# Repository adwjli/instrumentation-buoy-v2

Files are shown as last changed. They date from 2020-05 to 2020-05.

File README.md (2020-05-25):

# Instrumentation Buoy Data Logger - Version 2

A continuation of the [Instrumentation Buoy Data Logger (Version 1)](https://github.com/andrewjunli/instrumentation-buoy-v1) project, Version 2 features a new PCB layout where the electronics of the Main Board and Power Board are combined into one PCB assembly to make it easier to assemble the buoy. Improvements were made to the solar charging circuitry, a new wireless module has been used and the LED safety light has been redesigned. Also for the first time, I've published the full technical documentation of this design as a learning and reference resource for other hardware designers.

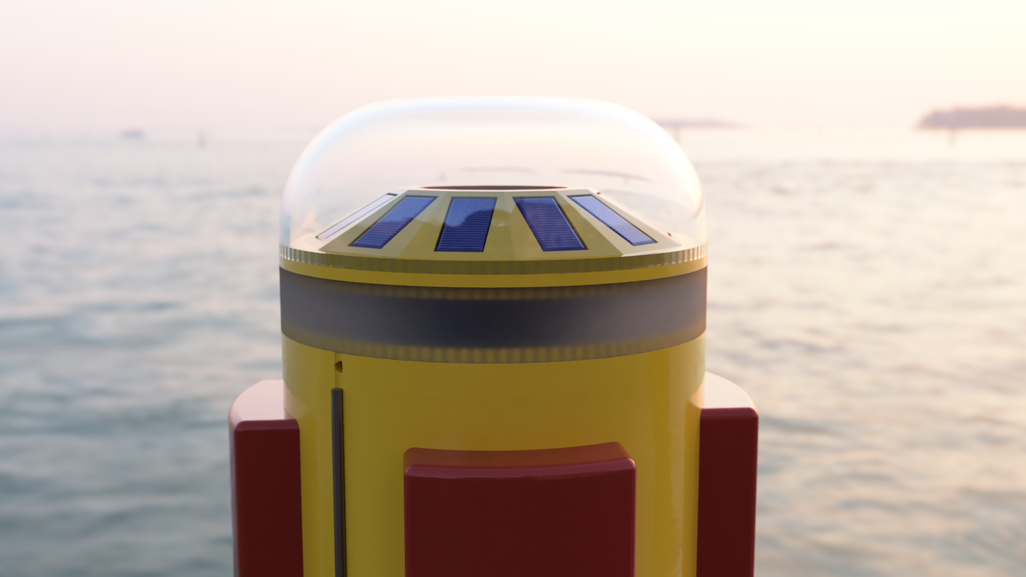
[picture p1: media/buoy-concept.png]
Buoy concept.


The imagery shown above is a concept design of the new buoy prototype.

## Technical Documentation

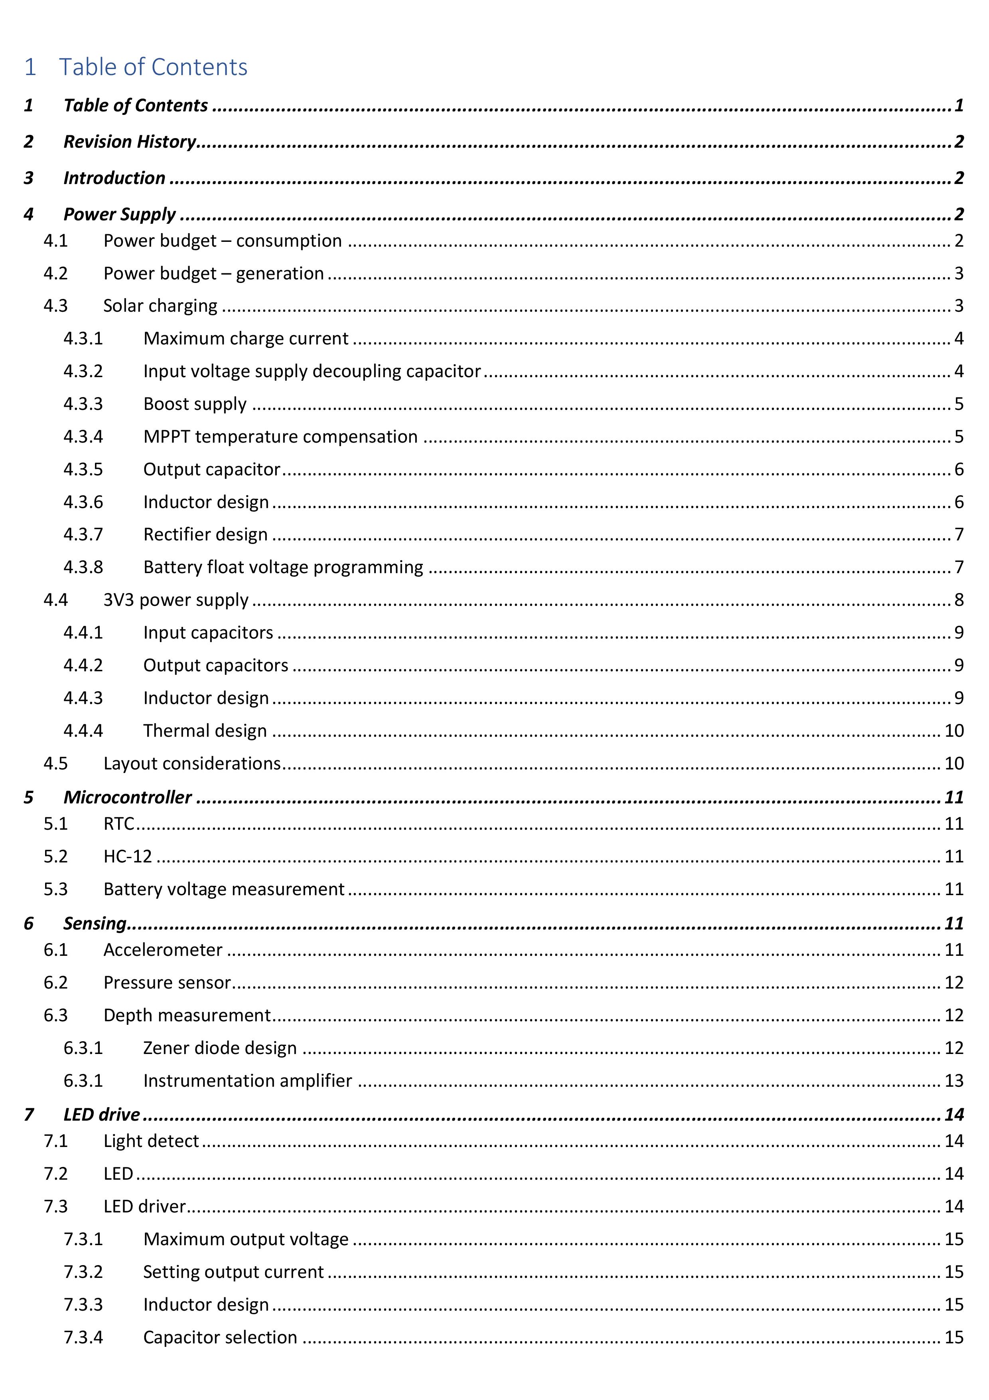
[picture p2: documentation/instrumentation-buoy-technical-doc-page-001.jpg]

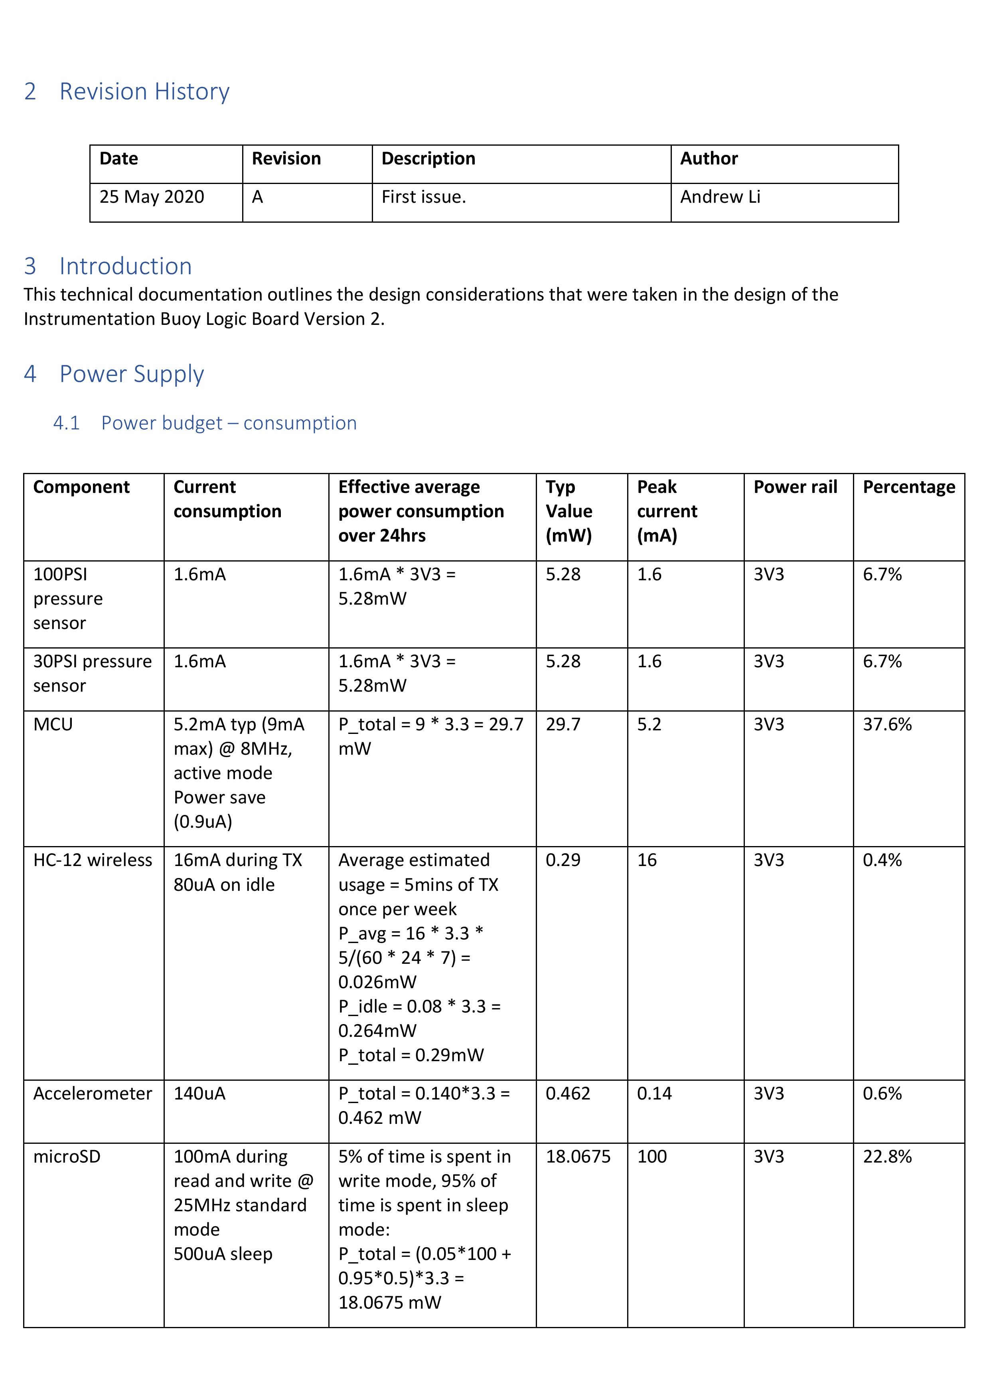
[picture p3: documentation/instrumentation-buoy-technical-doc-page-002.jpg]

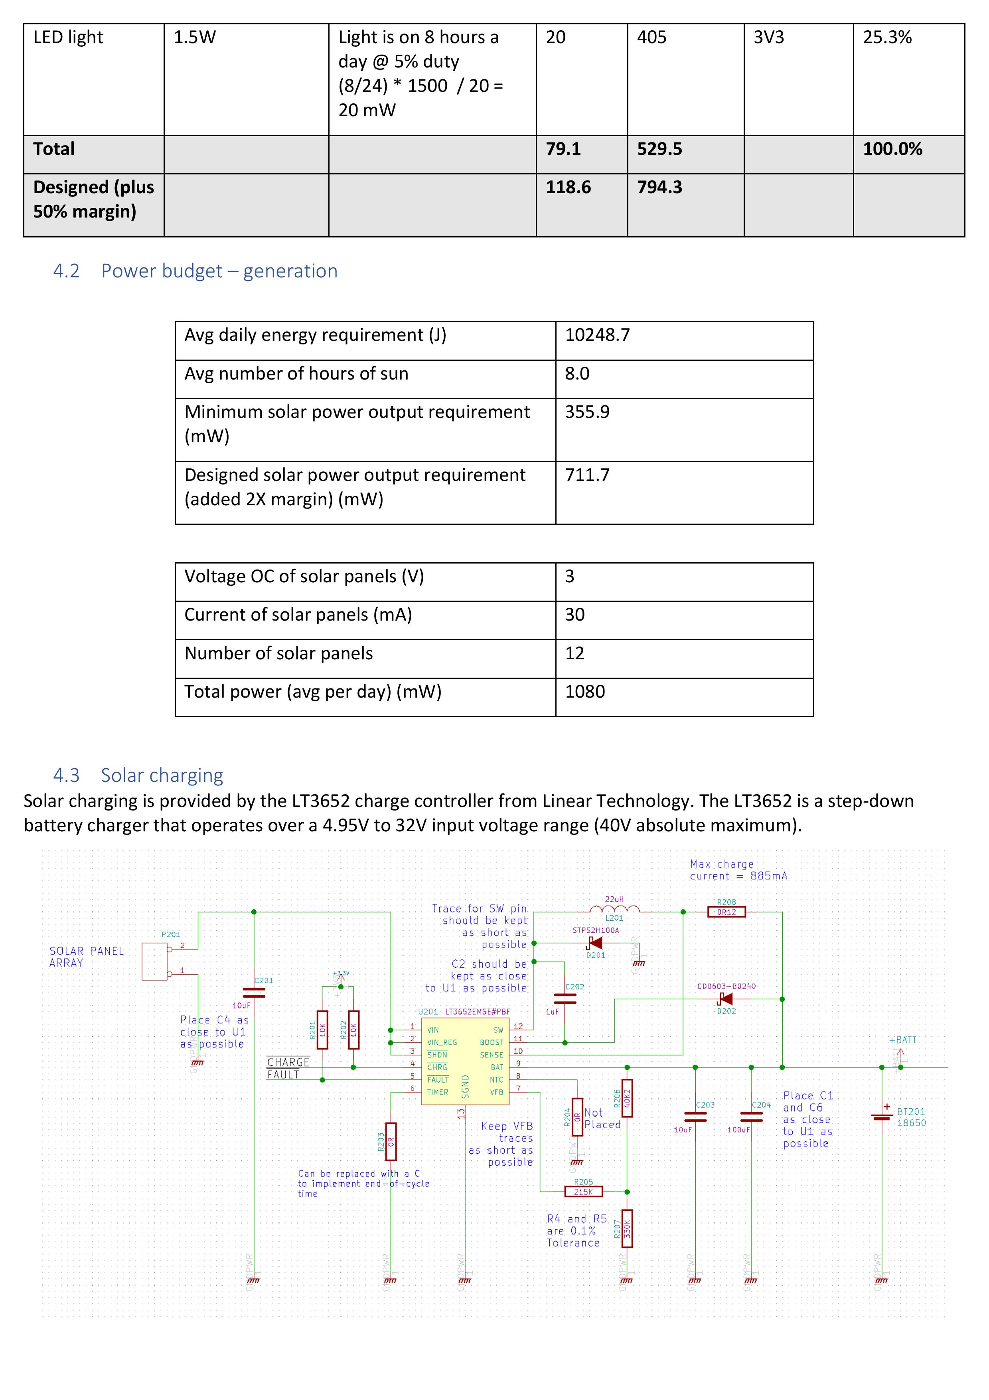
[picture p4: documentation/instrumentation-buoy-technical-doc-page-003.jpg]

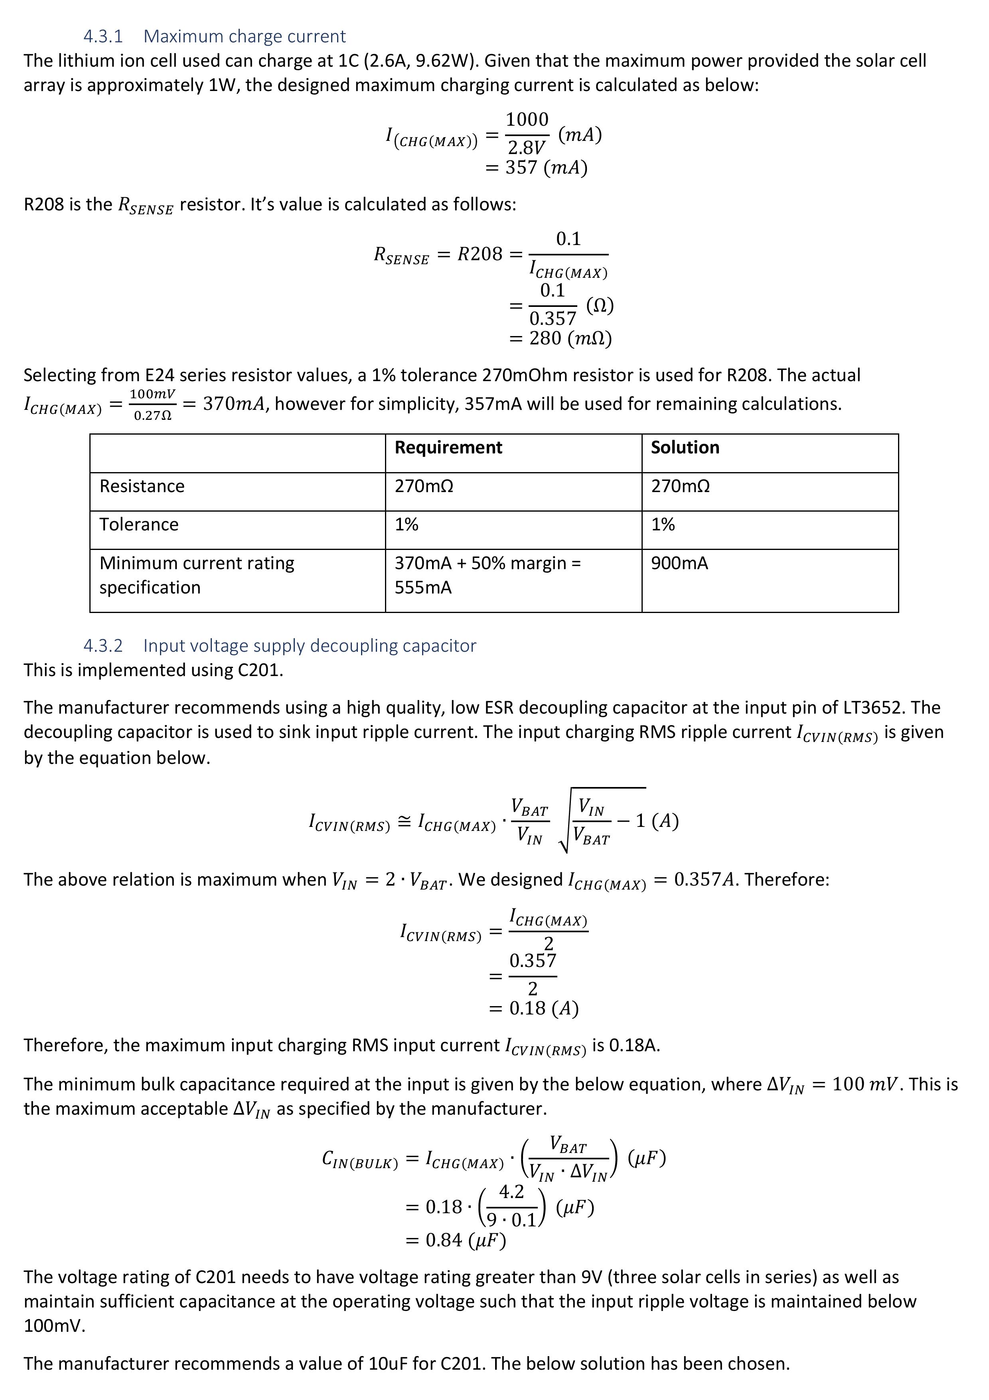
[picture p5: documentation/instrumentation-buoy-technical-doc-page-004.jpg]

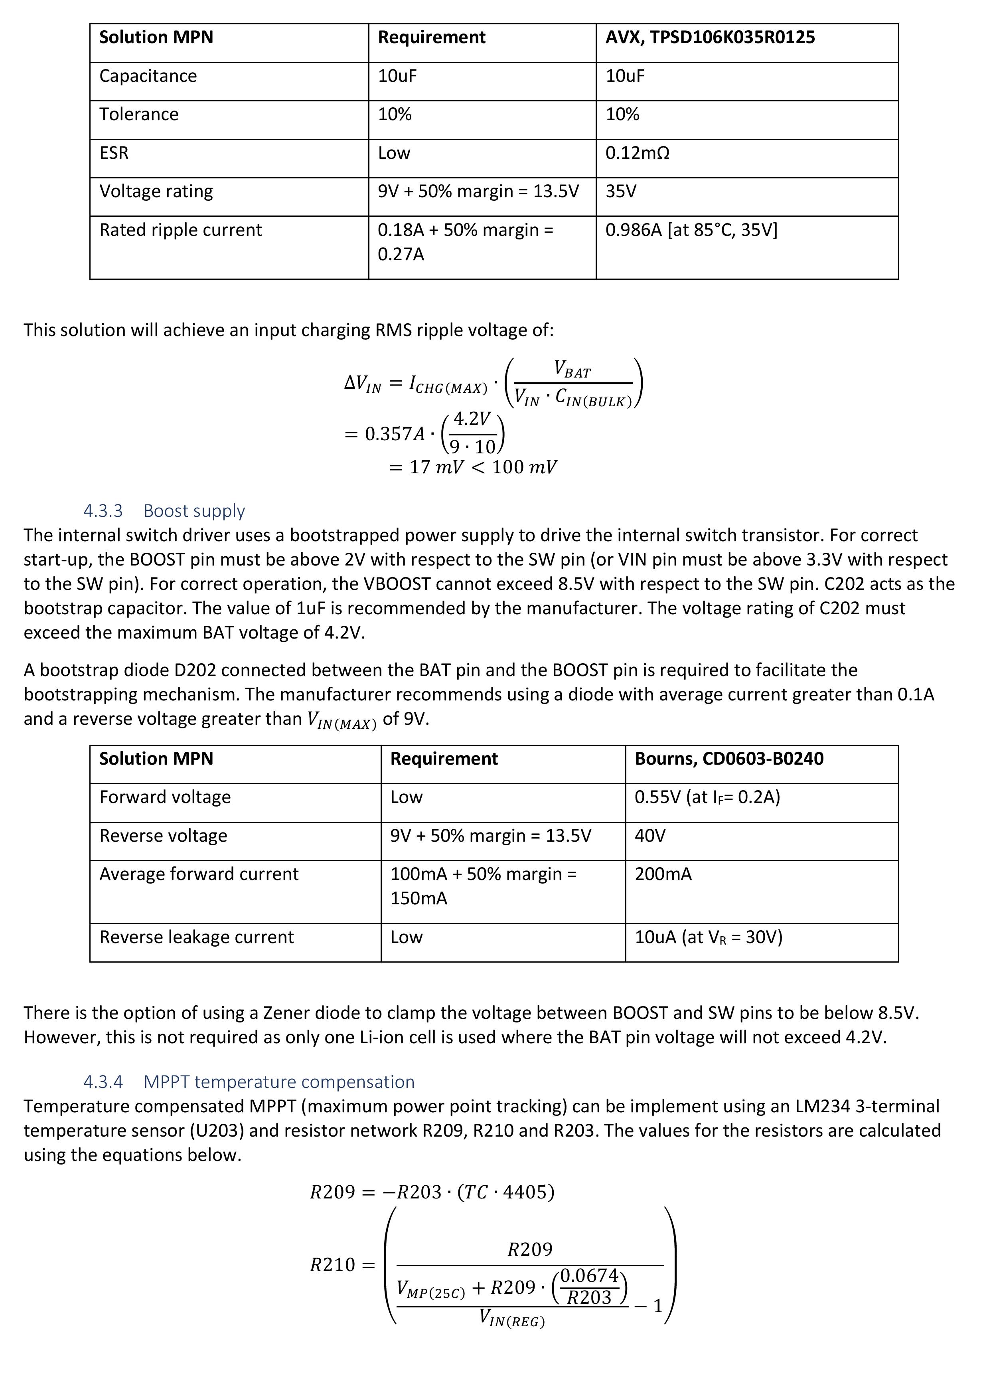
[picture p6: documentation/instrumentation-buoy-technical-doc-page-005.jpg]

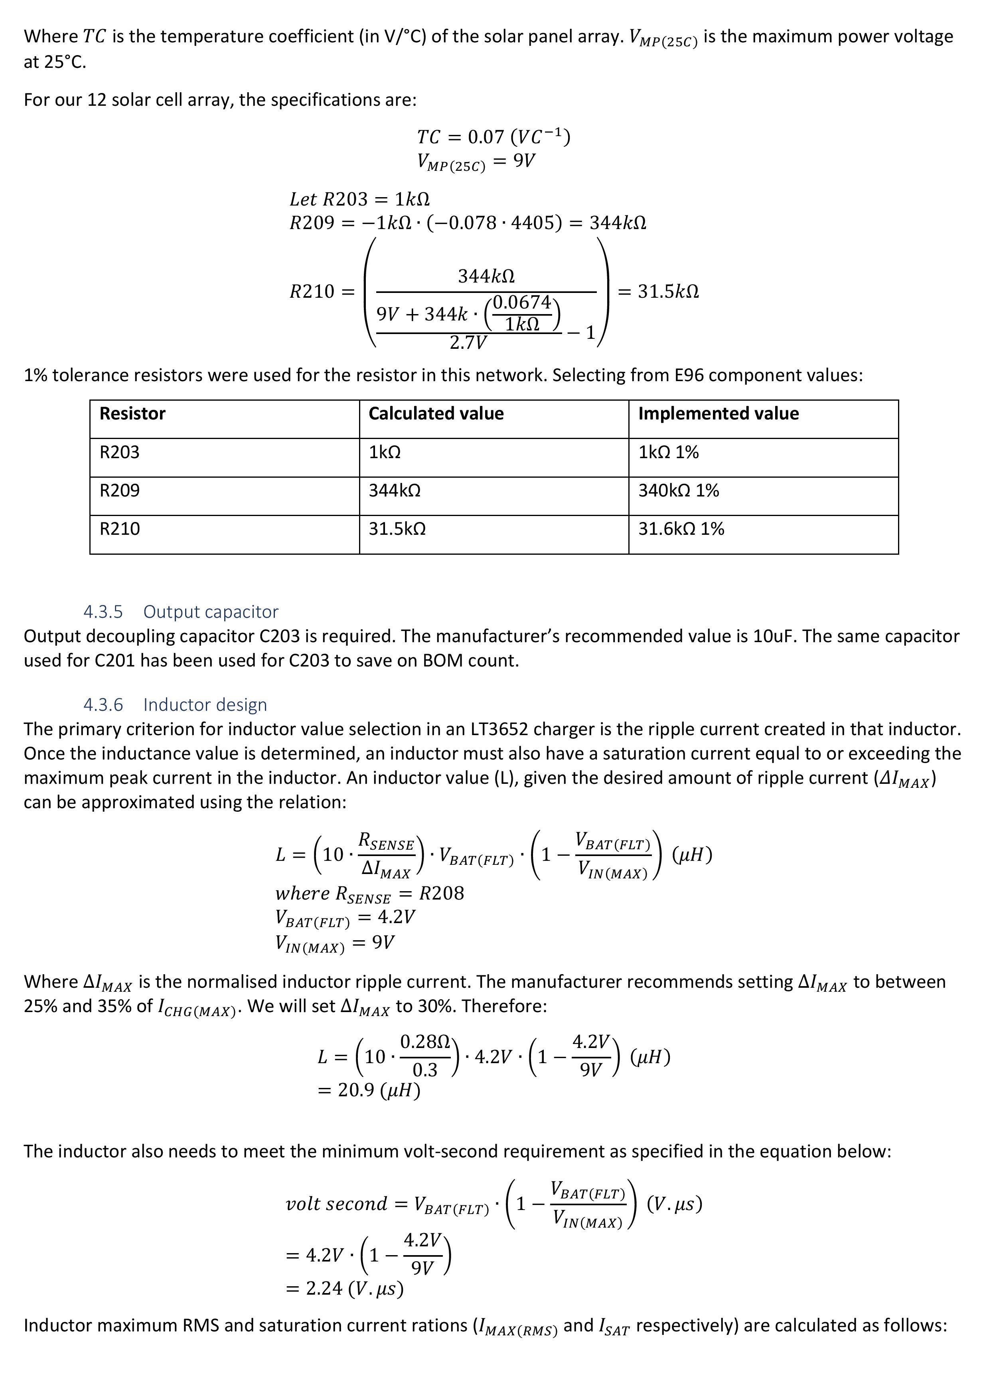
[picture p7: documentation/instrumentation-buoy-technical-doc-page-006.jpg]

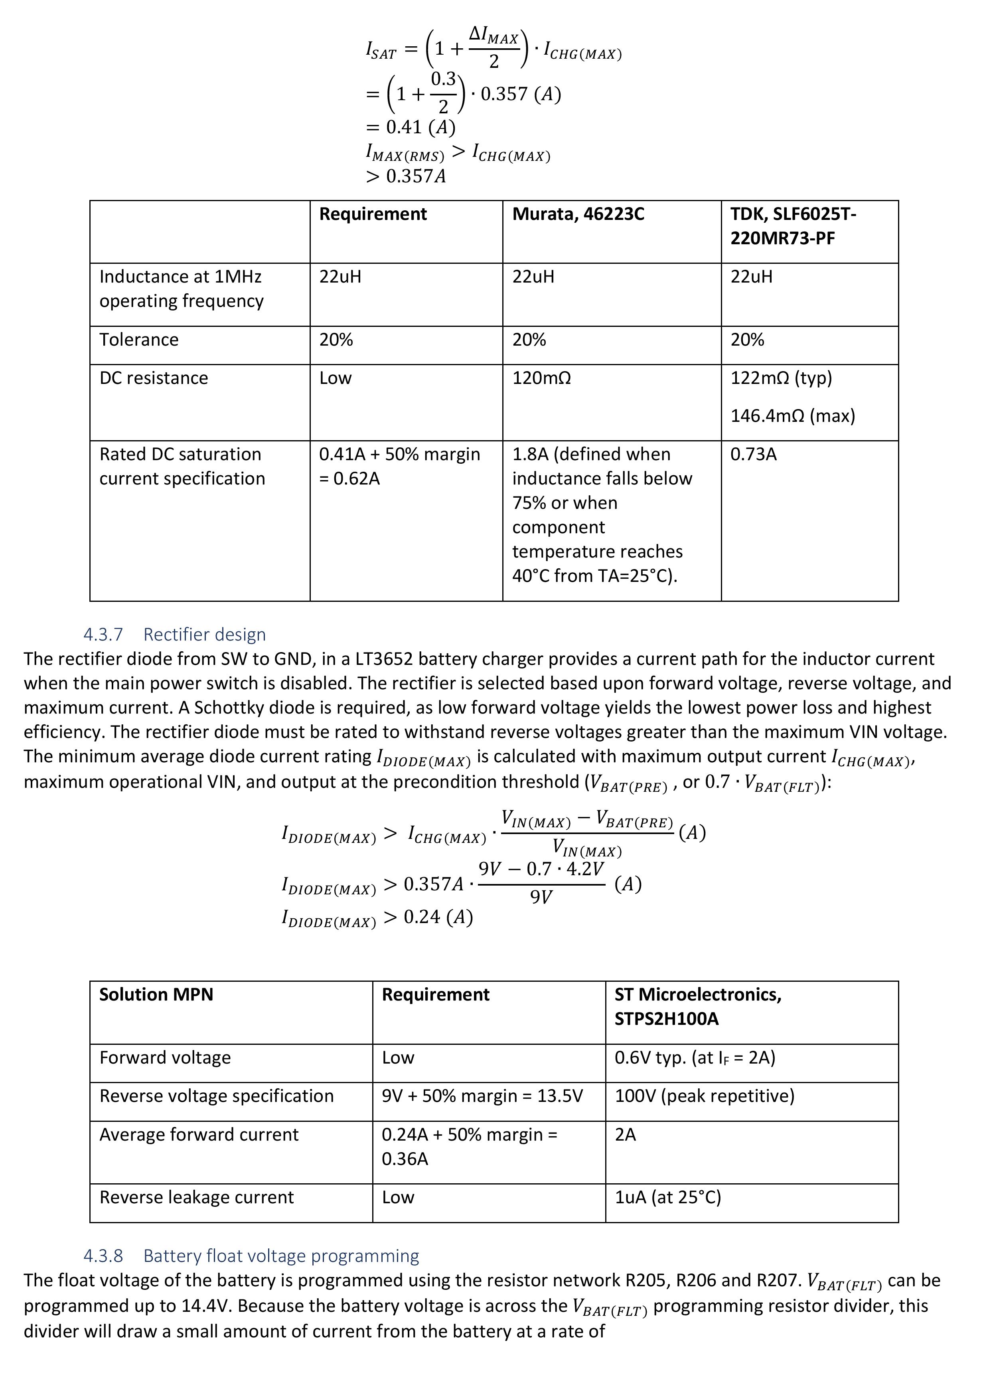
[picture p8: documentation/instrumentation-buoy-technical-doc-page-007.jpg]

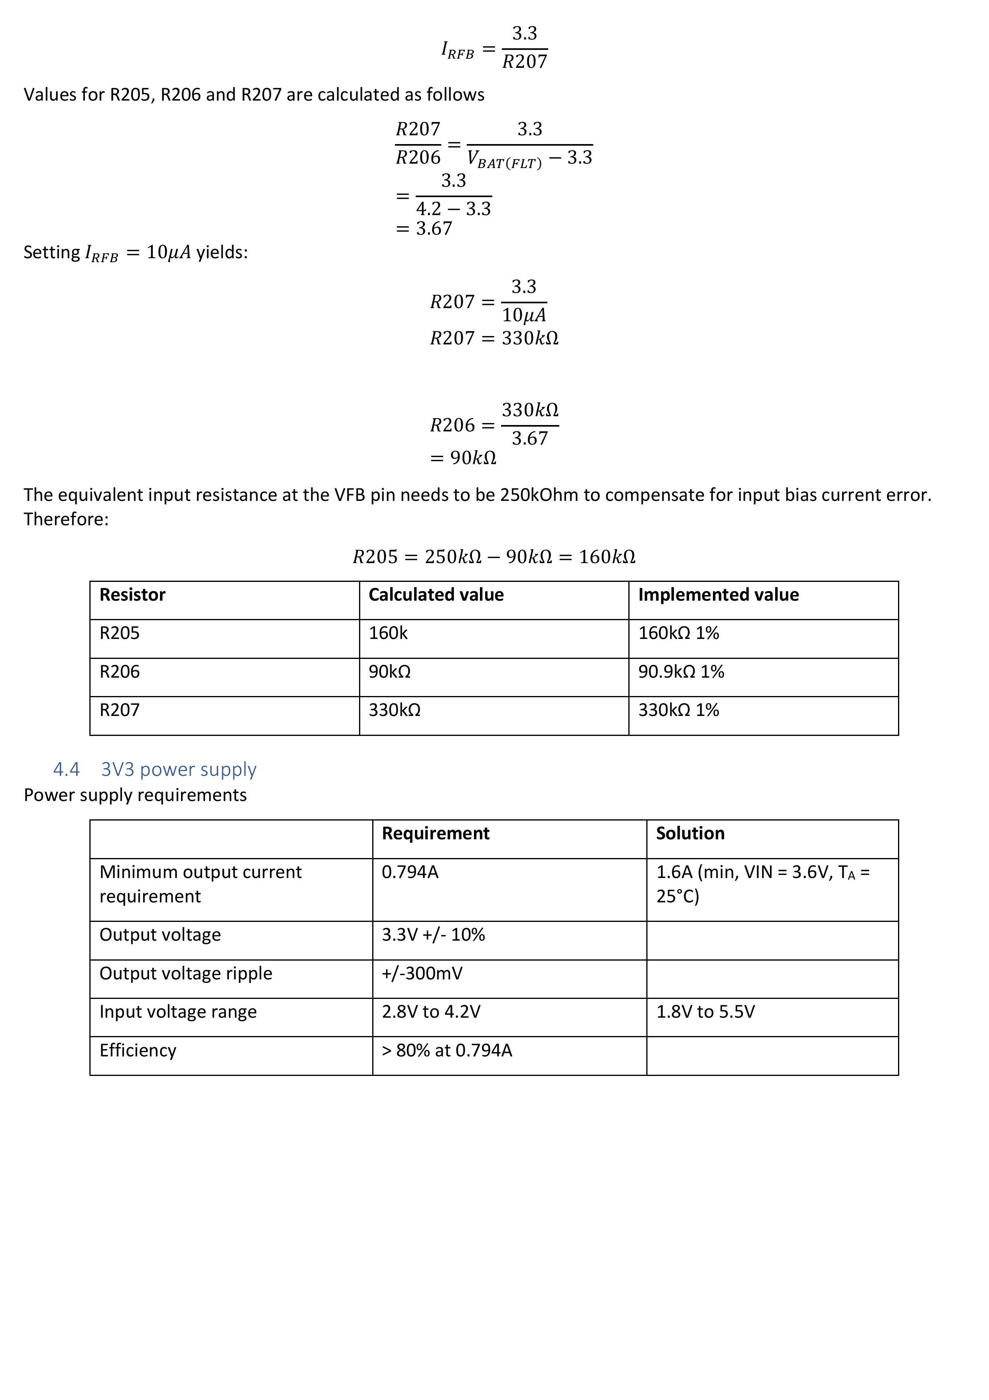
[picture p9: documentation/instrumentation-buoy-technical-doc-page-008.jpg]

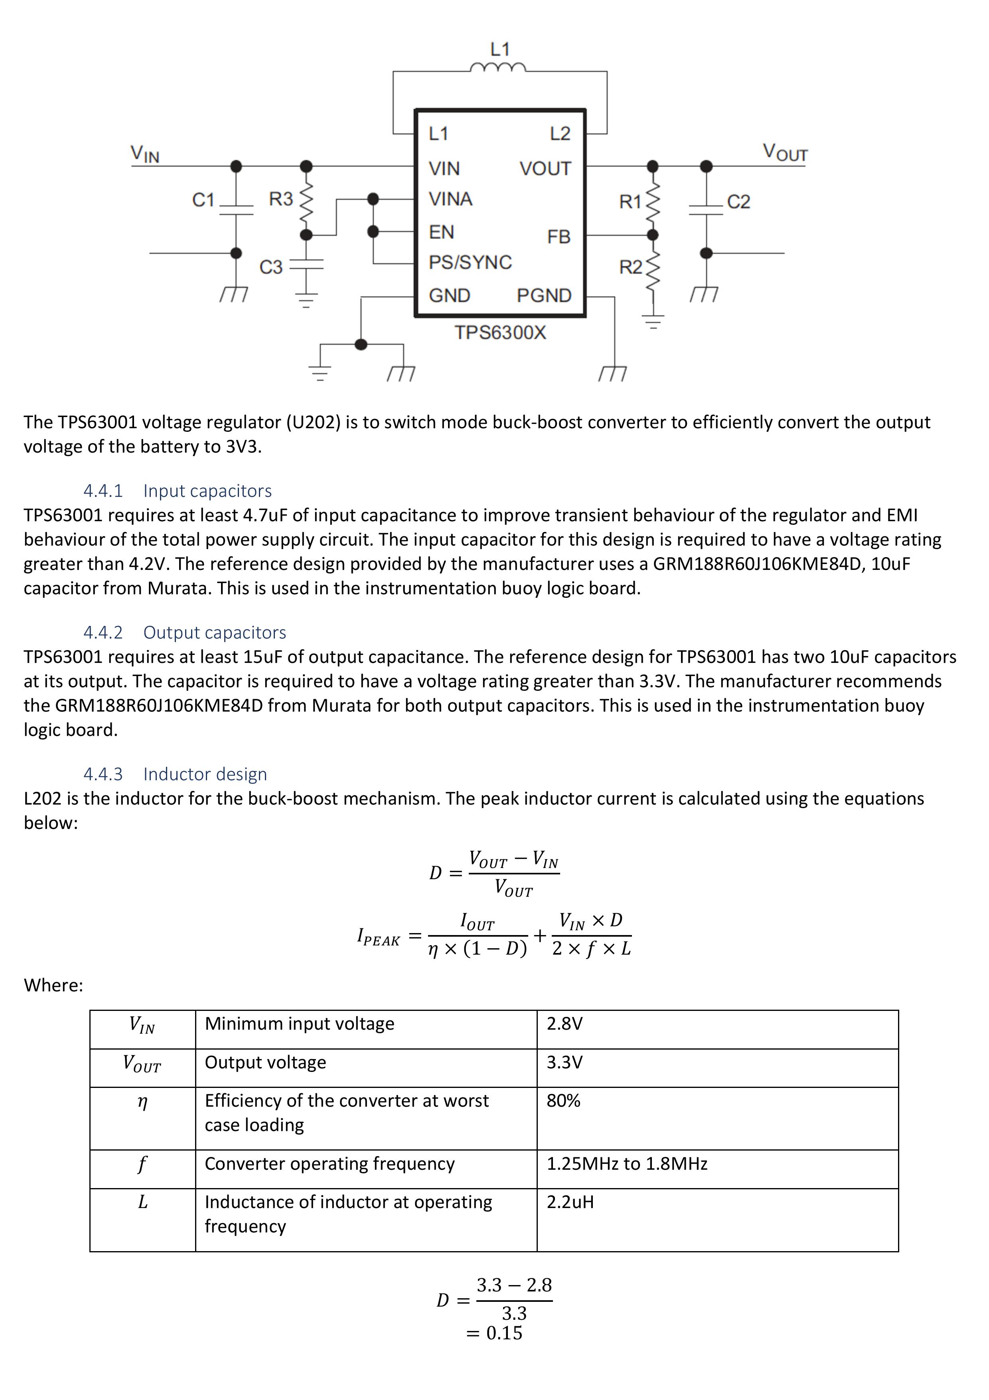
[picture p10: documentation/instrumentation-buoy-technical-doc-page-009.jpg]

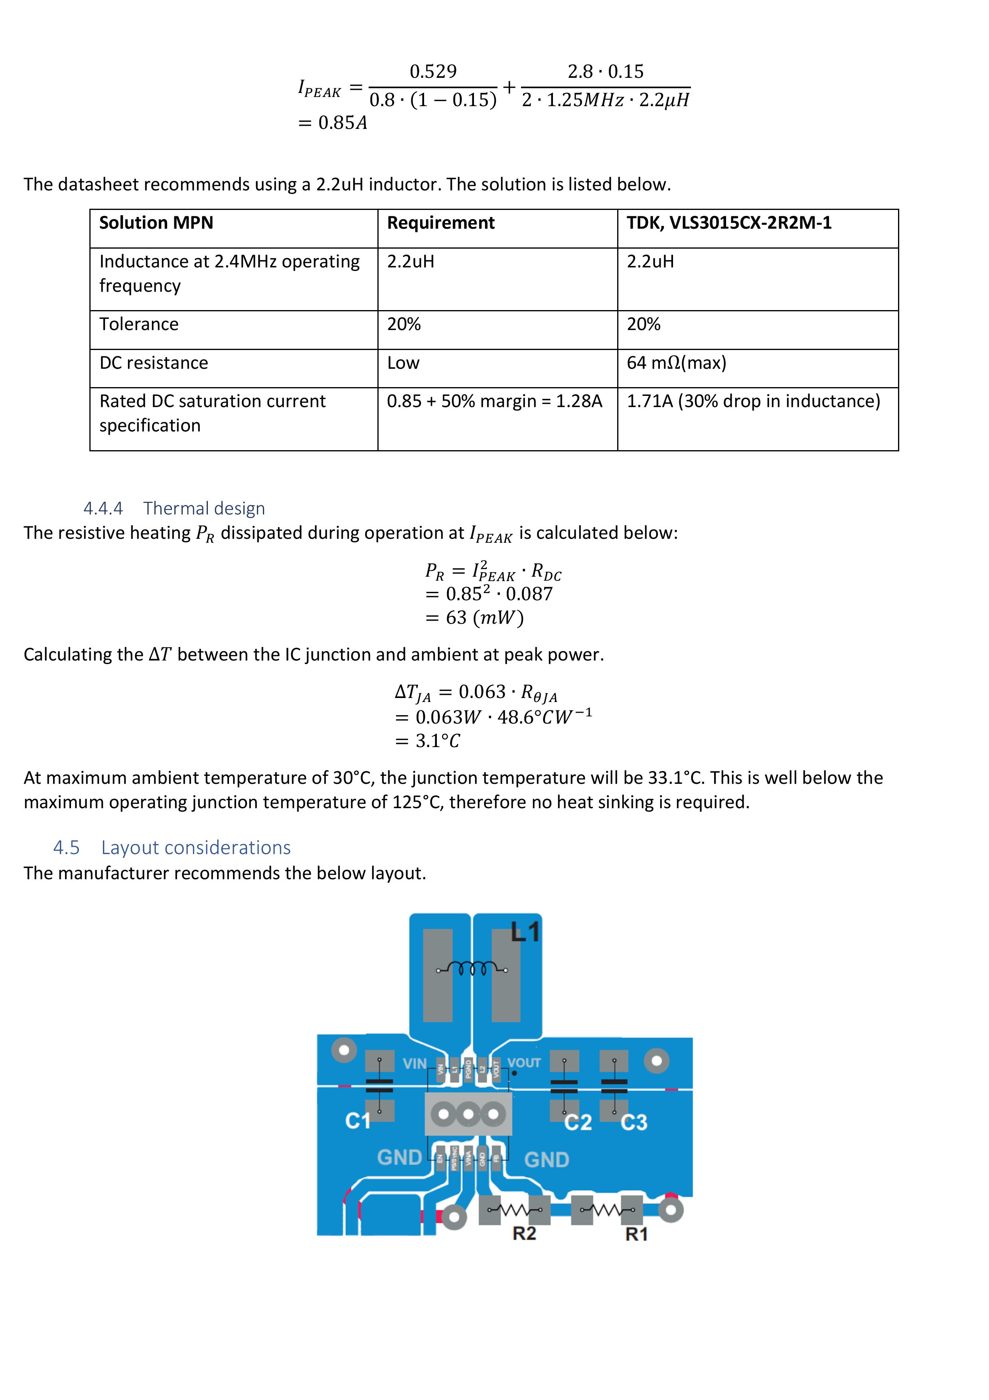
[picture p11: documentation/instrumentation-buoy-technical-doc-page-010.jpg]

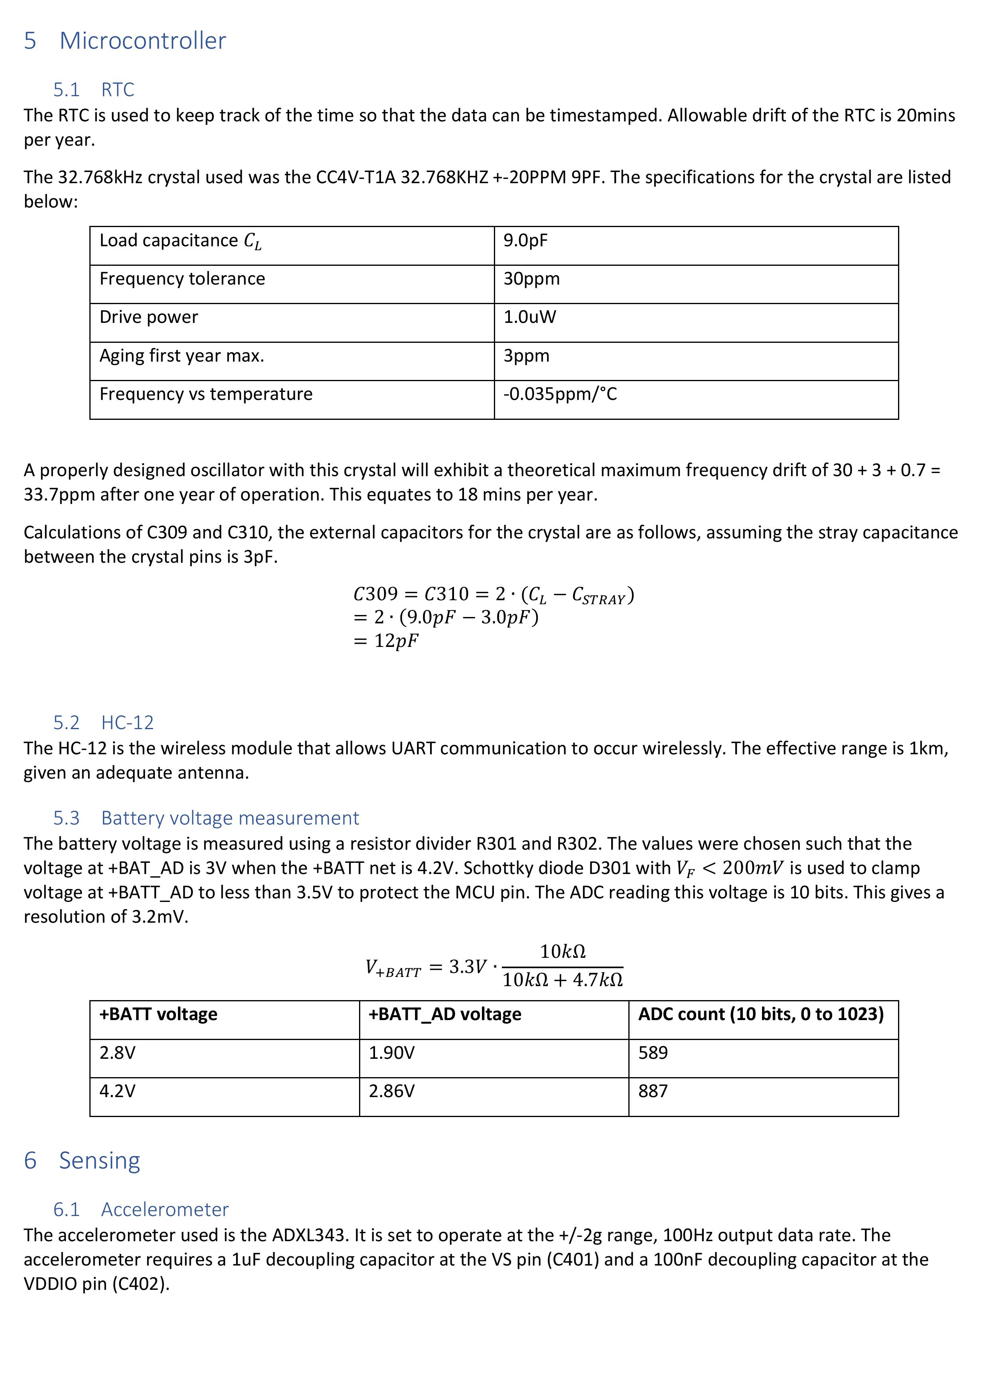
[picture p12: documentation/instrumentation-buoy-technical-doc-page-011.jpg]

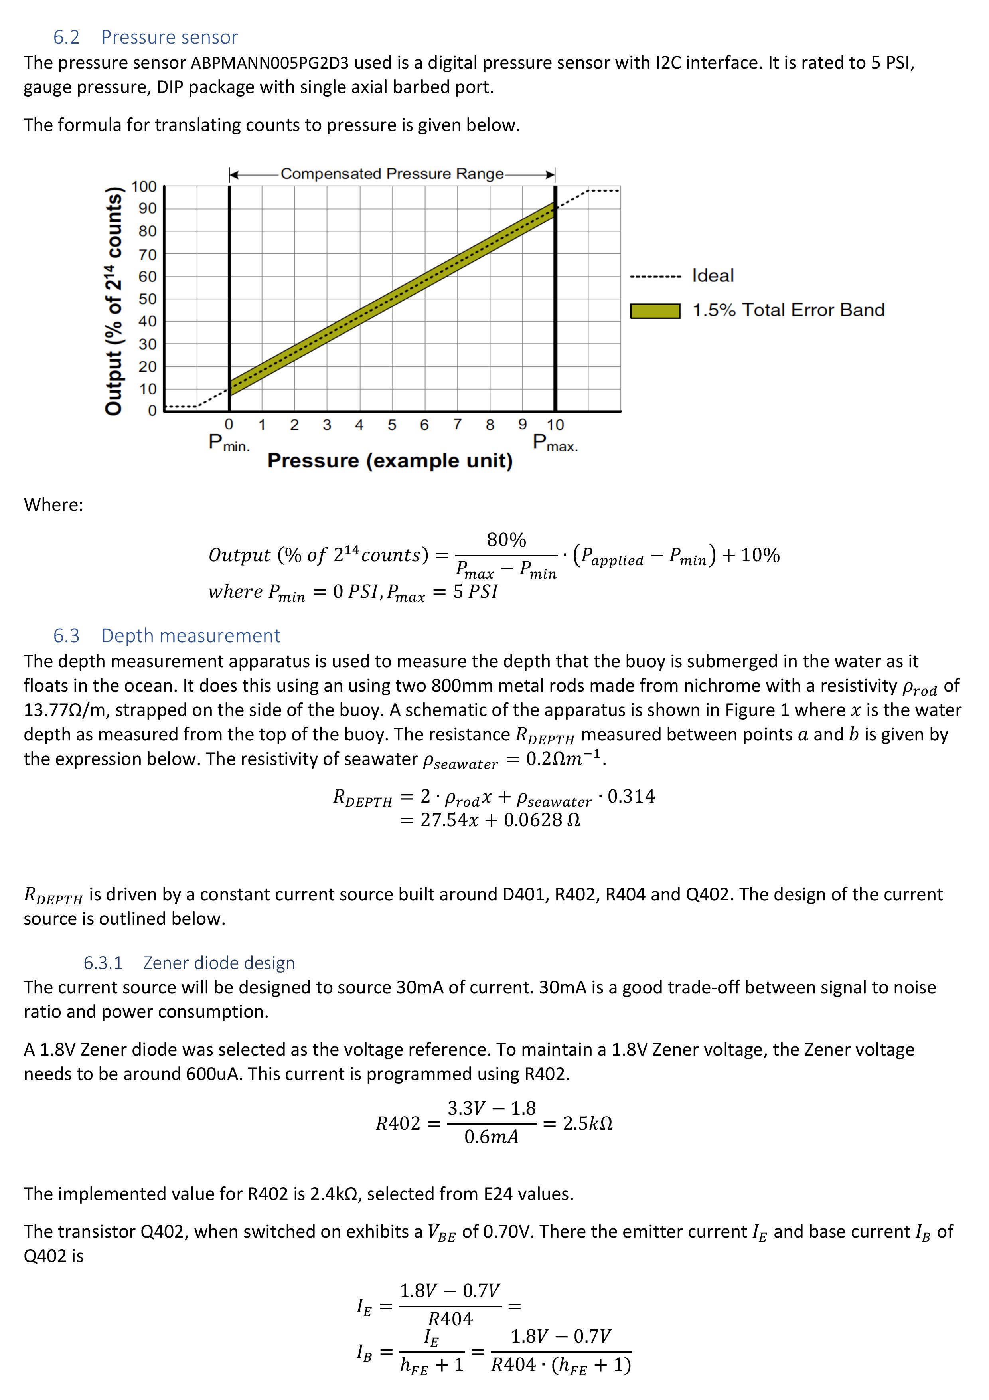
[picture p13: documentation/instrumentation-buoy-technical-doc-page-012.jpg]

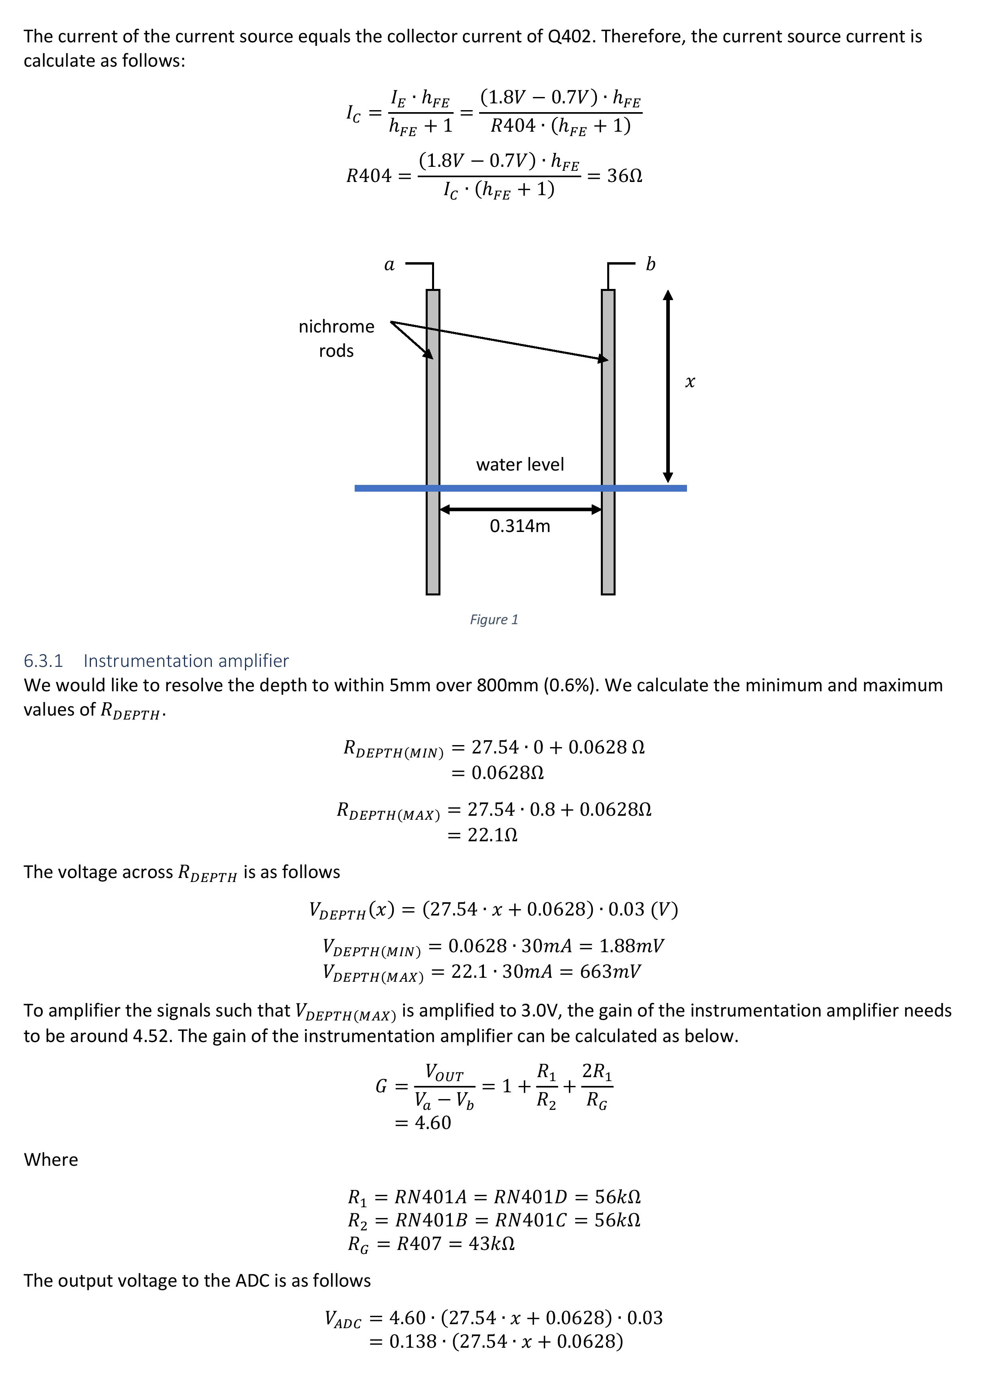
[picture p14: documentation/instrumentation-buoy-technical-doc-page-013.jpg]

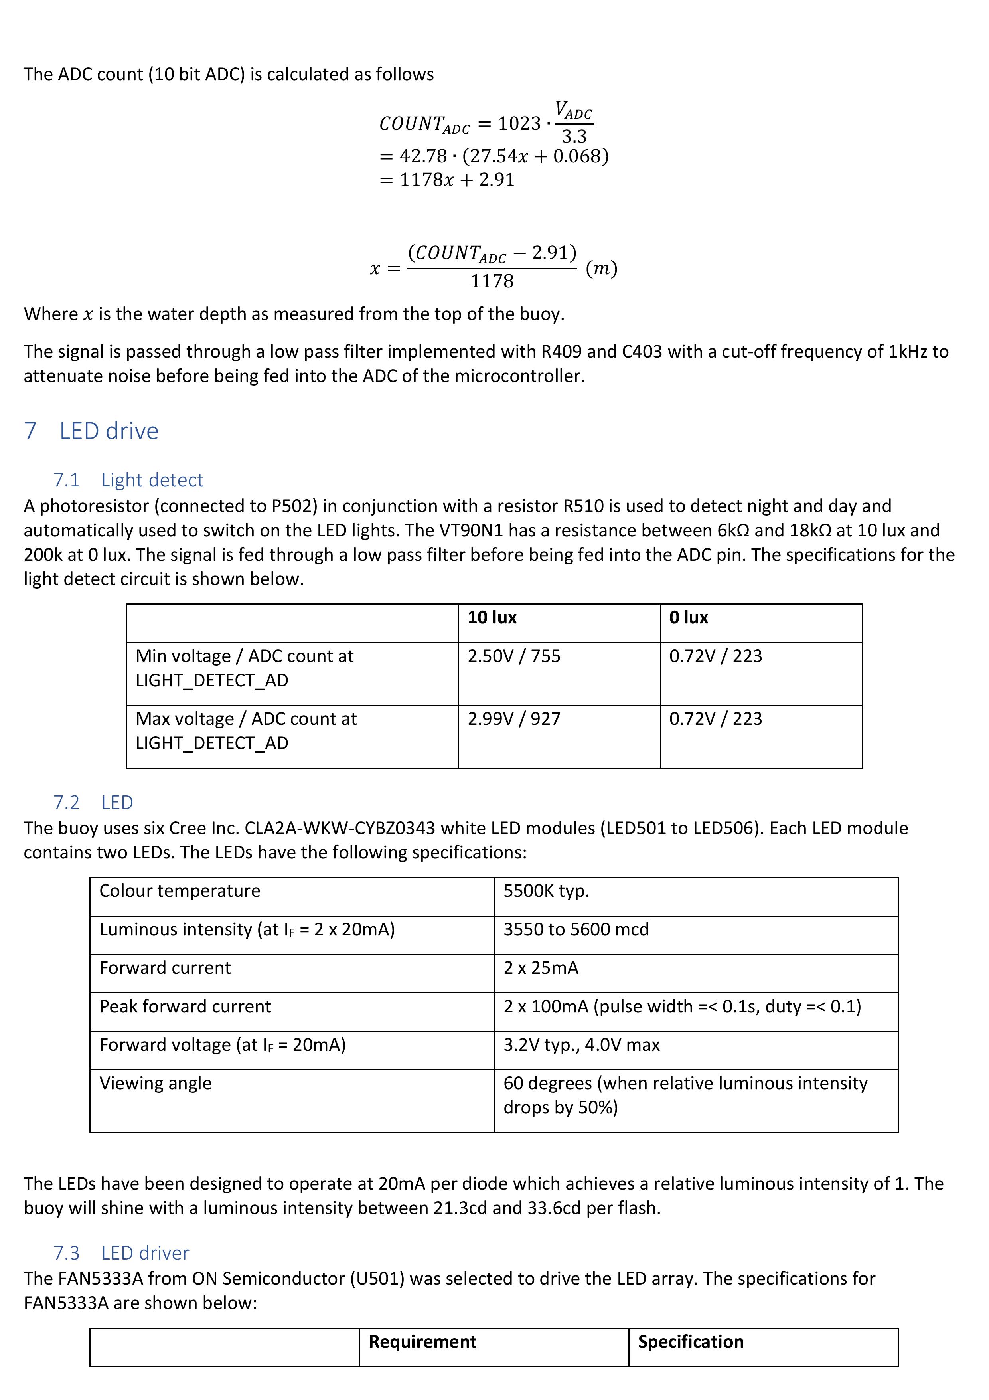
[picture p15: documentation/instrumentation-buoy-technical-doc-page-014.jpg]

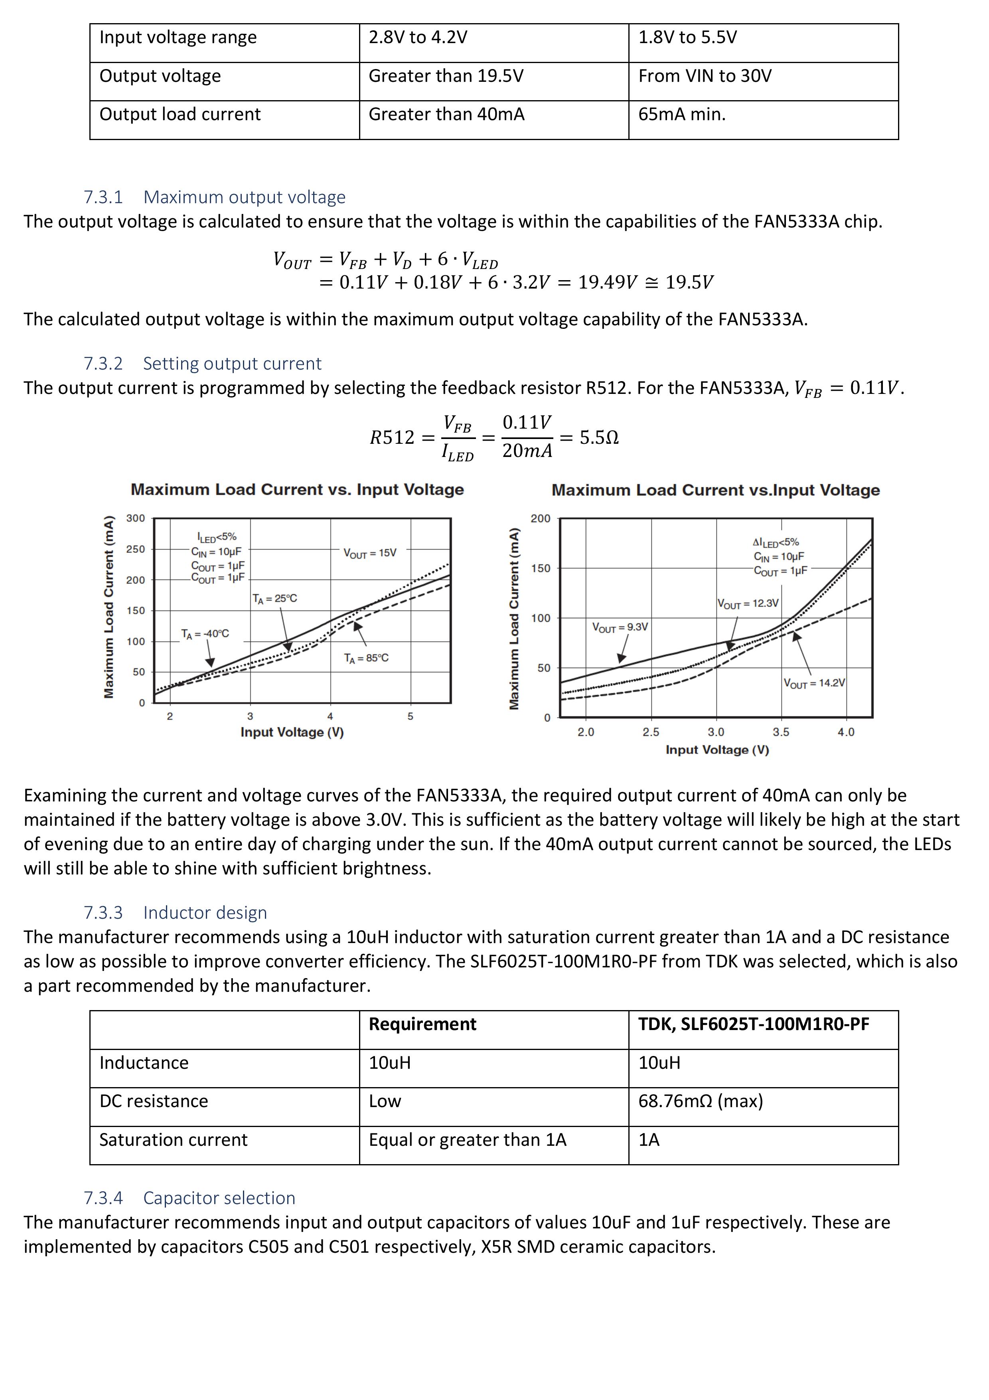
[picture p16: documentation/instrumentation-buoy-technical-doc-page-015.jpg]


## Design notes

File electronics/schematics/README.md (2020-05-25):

# Schematics

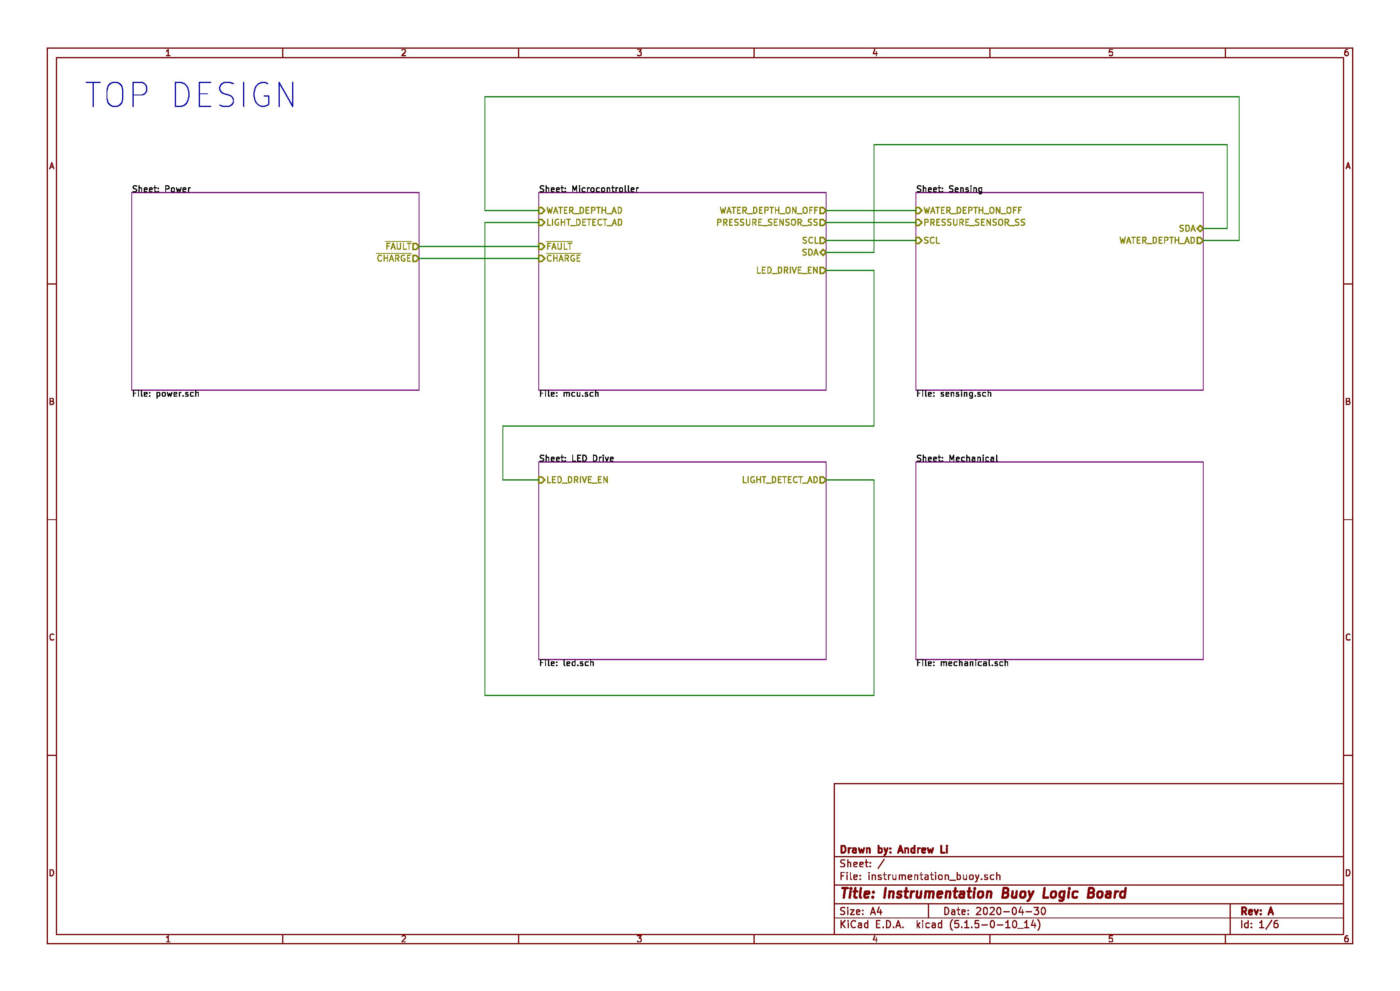
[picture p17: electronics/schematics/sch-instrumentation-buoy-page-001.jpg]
Schematics of Instrumentation Buoy Version 2.


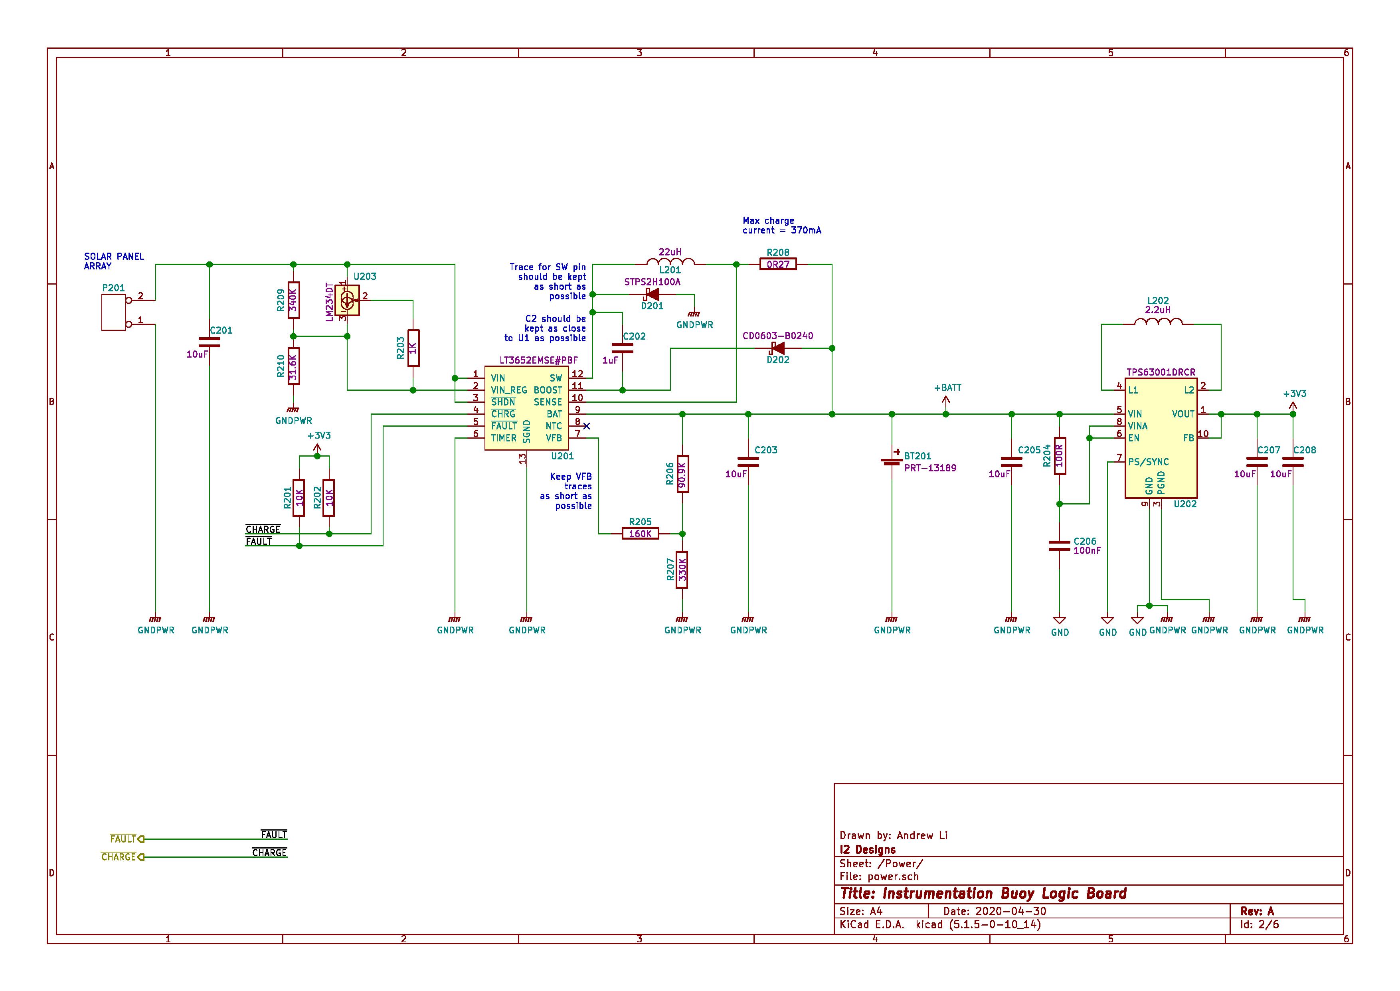
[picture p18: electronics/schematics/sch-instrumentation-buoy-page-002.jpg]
Schematics of Instrumentation Buoy Version 2.


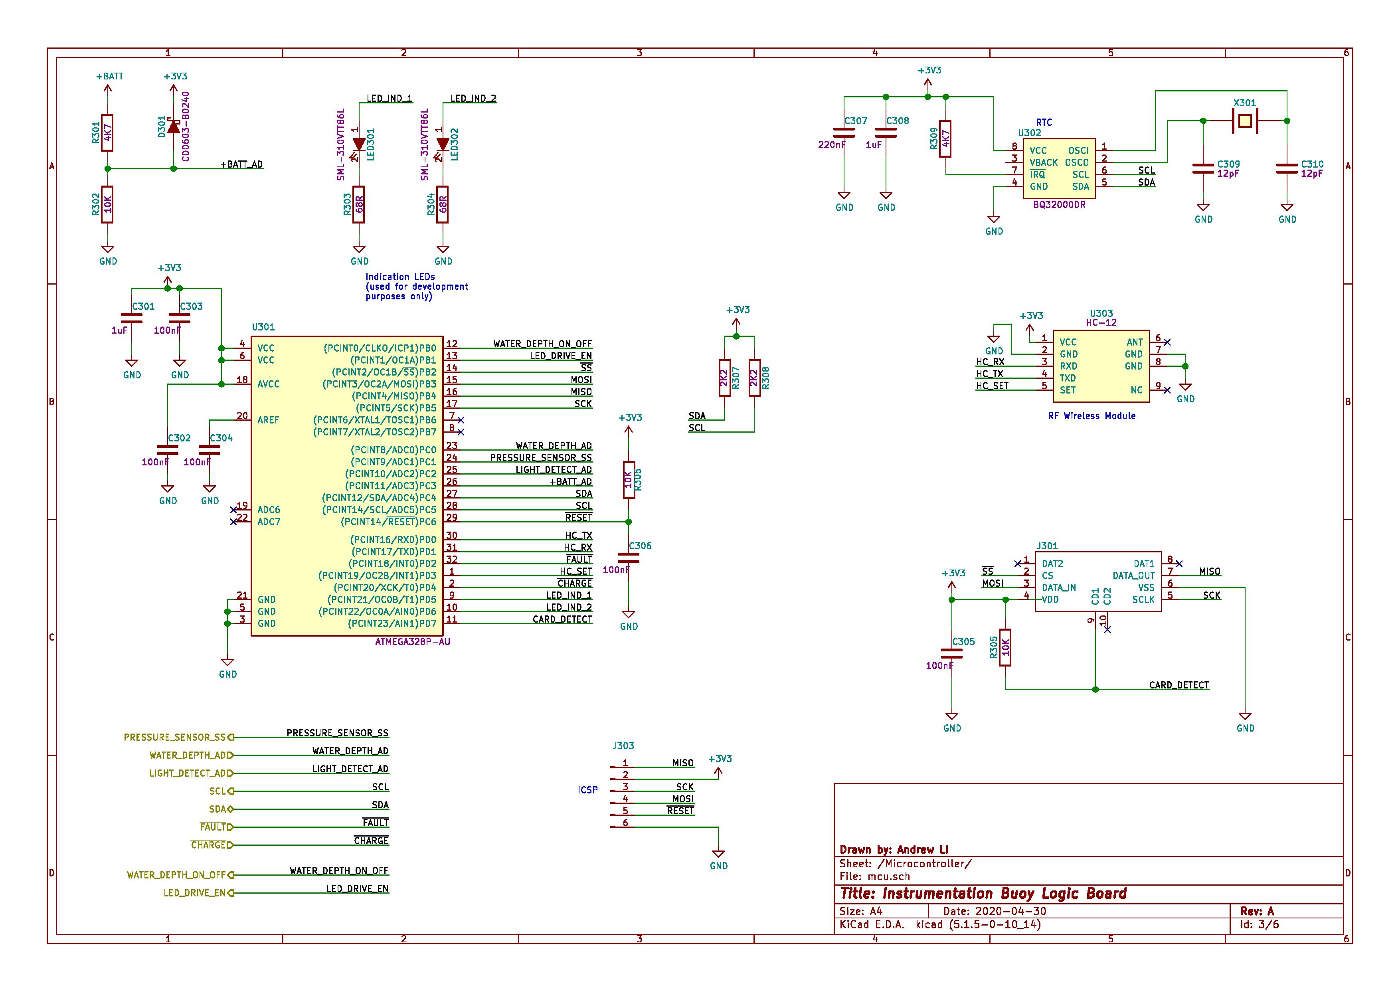
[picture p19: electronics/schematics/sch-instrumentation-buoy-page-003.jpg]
Schematics of Instrumentation Buoy Version 2.


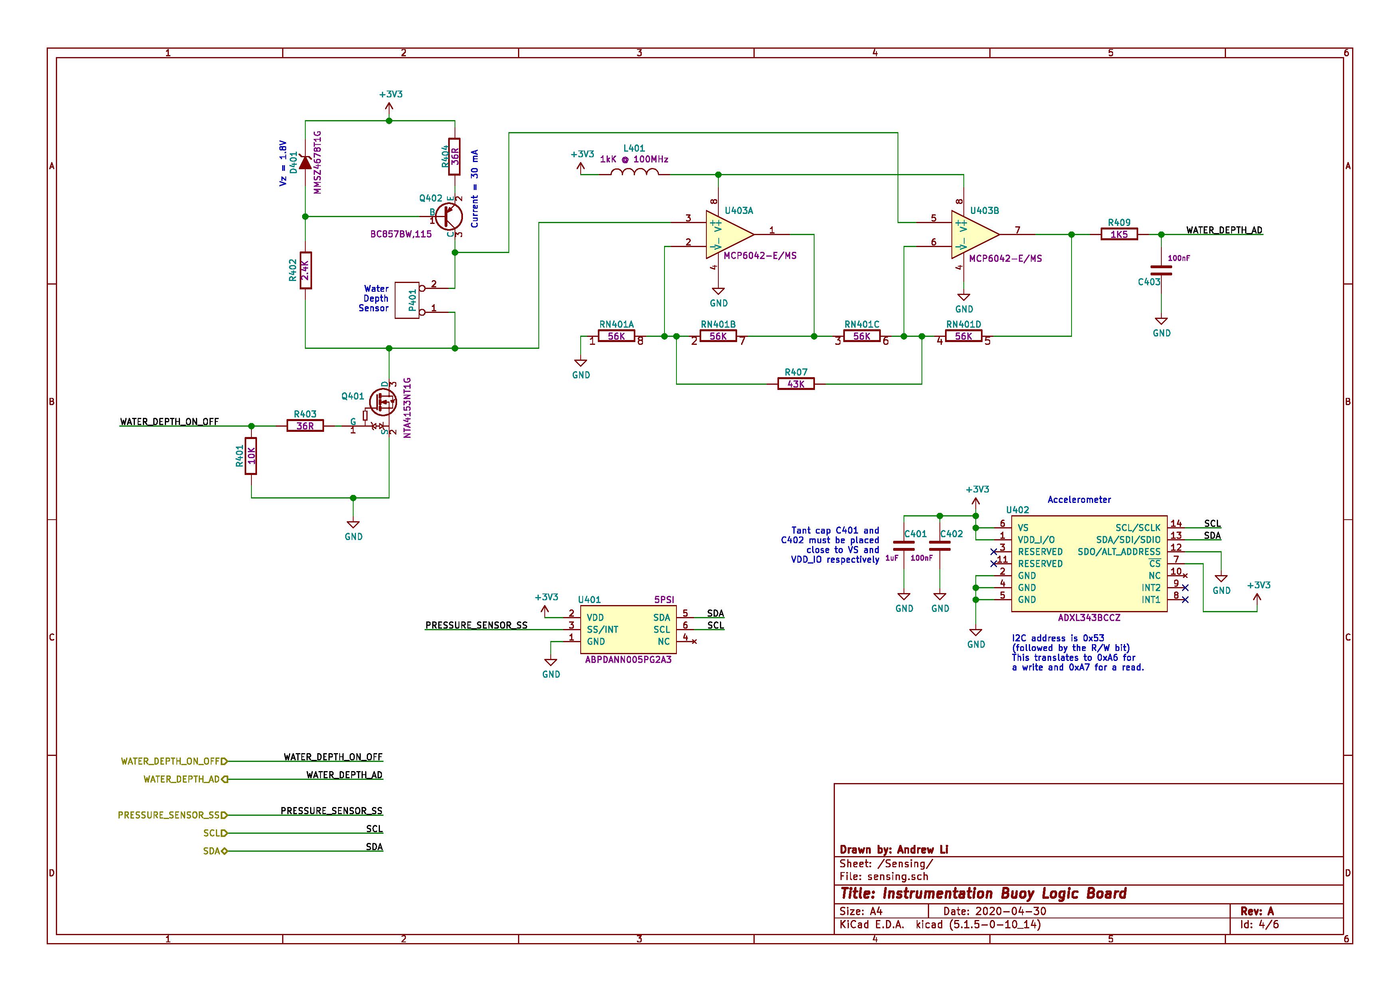
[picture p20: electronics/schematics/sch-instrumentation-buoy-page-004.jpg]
Schematics of Instrumentation Buoy Version 2.


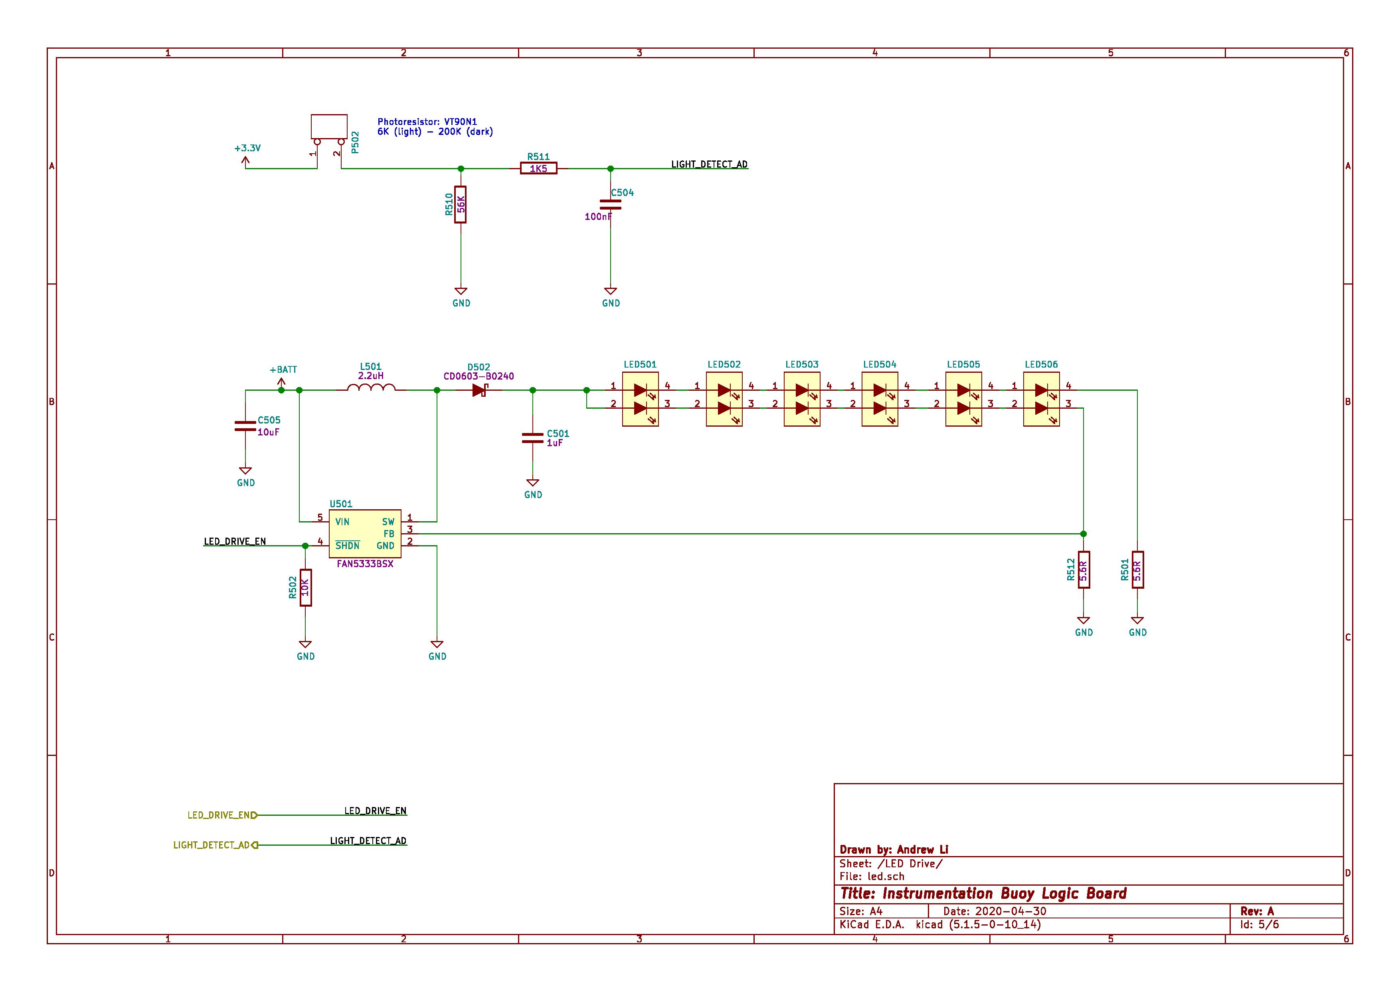
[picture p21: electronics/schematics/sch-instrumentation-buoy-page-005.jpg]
Schematics of Instrumentation Buoy Version 2.


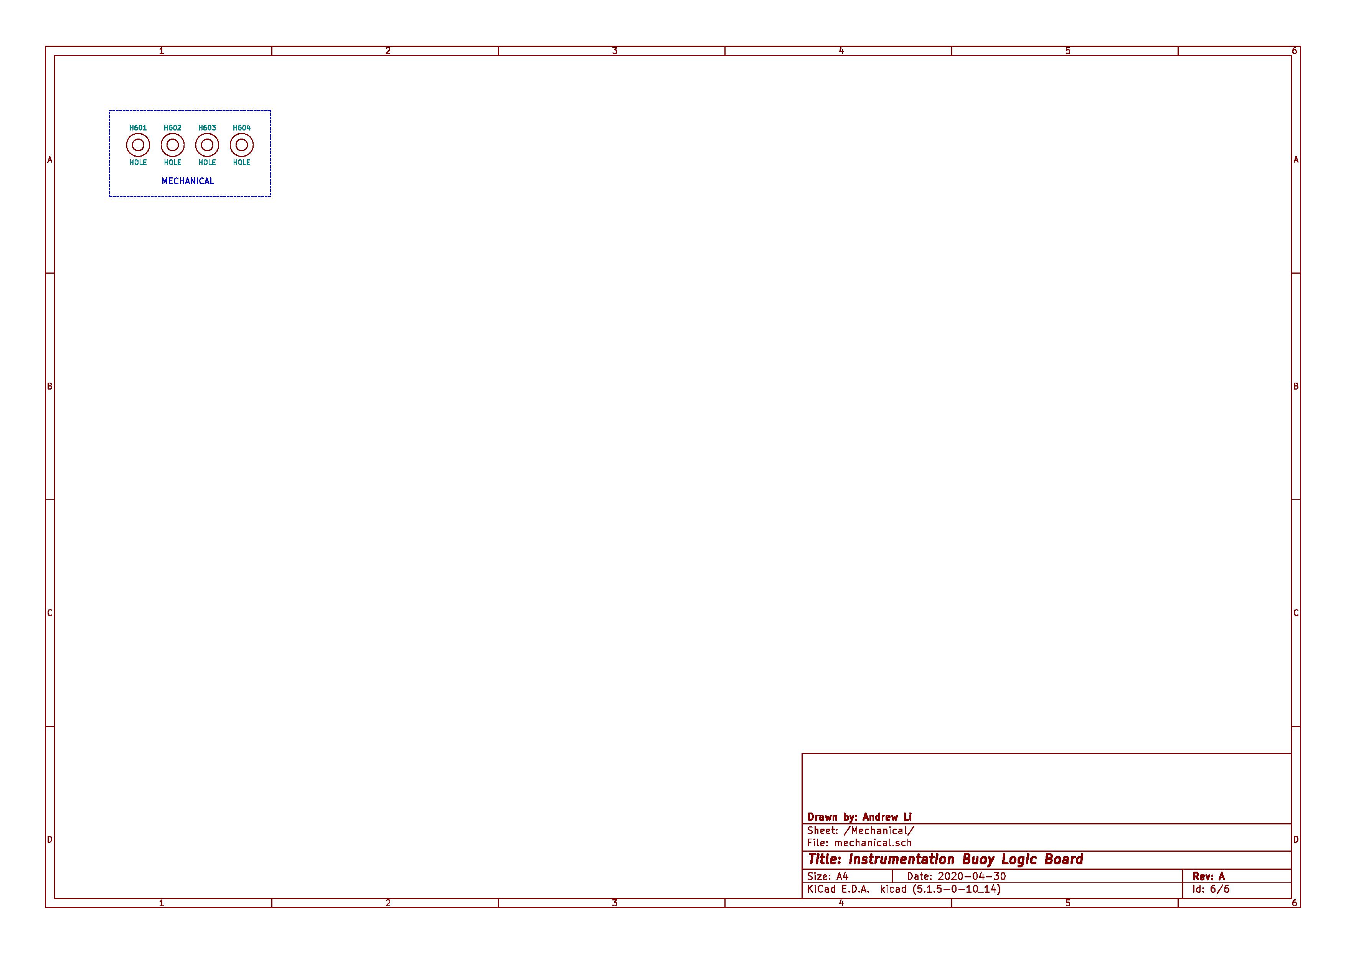
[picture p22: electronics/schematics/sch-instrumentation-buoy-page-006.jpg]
Schematics of Instrumentation Buoy Version 2.


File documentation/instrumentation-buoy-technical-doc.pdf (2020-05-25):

## 1 Table of Contents

## 2 Revision History

Date | Revision | Description | Author
25 May 2020 | A | First issue. | Andrew Li

## 3 Introduction

This technical documentation outlines the design considerations that were taken in the design of the Instrumentation Buoy Logic Board Version 2.

## 4 Power Supply

4.1 Power budget – consumption

Component | Current consumption | Effective average power consumption over 24hrs | Typ Value (mW) | Peak current (mA) | Power rail | Percentage
100PSI pressure sensor | 1.6mA | 1.6mA * 3V3 = 5.28mW | 5.28 | 1.6 | 3V3 | 6.7%
30PSI pressure sensor | 1.6mA | 1.6mA * 3V3 = 5.28mW | 5.28 | 1.6 | 3V3 | 6.7%
MCU | 5.2mA typ (9mA max) @ 8MHz, active mode Power save (0.9uA) | P_total = 9 * 3.3 = 29.7 mW | 29.7 | 5.2 | 3V3 | 37.6%
HC-12 wireless | 16mA during TX 80uA on idle | Average estimated usage = 5mins of TX once per week P_avg = 16 * 3.3 * 5/(60 * 24 * 7) = 0.026mW P_idle = 0.08 * 3.3 = 0.264mW P_total = 0.29mW | 0.29 | 16 | 3V3 | 0.4%
Accelerometer | 140uA | P_total = 0.140*3.3 = 0.462 mW | 0.462 | 0.14 | 3V3 | 0.6%
microSD | 100mA during read and write @ 25MHz standard mode 500uA sleep | 5% of time is spent in write mode, 95% of time is spent in sleep mode: P_total = (0.05*100 + 0.95*0.5)*3.3 = 18.0675 mW | 18.0675 | 100 | 3V3 | 22.8%

LED light | 1.5W | Light is on 8 hours a day @ 5% duty (8/24) * 1500 / 20 = 20 mW | 20 | 405 | 3V3 | 25.3%
Total | | | 79.1 | 529.5 | | 100.0%
Designed (plus 50% margin) | | | 118.6 794.3

4.2 Power budget – generation

Avg daily energy requirement (J) | 10248.7
Avg number of hours of sun | 8.0
Minimum solar power output requirement (mW) | 355.9
Designed solar power output requirement (added 2X margin) (mW) | 711.7
Voltage OC of solar panels (V) | 3
Current of solar panels (mA) | 30
Number of solar panels | 12
Total power (avg per day) (mW) | 1080

4.3 Solar charging
Solar charging is provided by the LT3652 charge controller from Linear Technology. The LT3652 is a step-down battery charger that operates over a 4.95V to 32V input voltage range (40V absolute maximum).

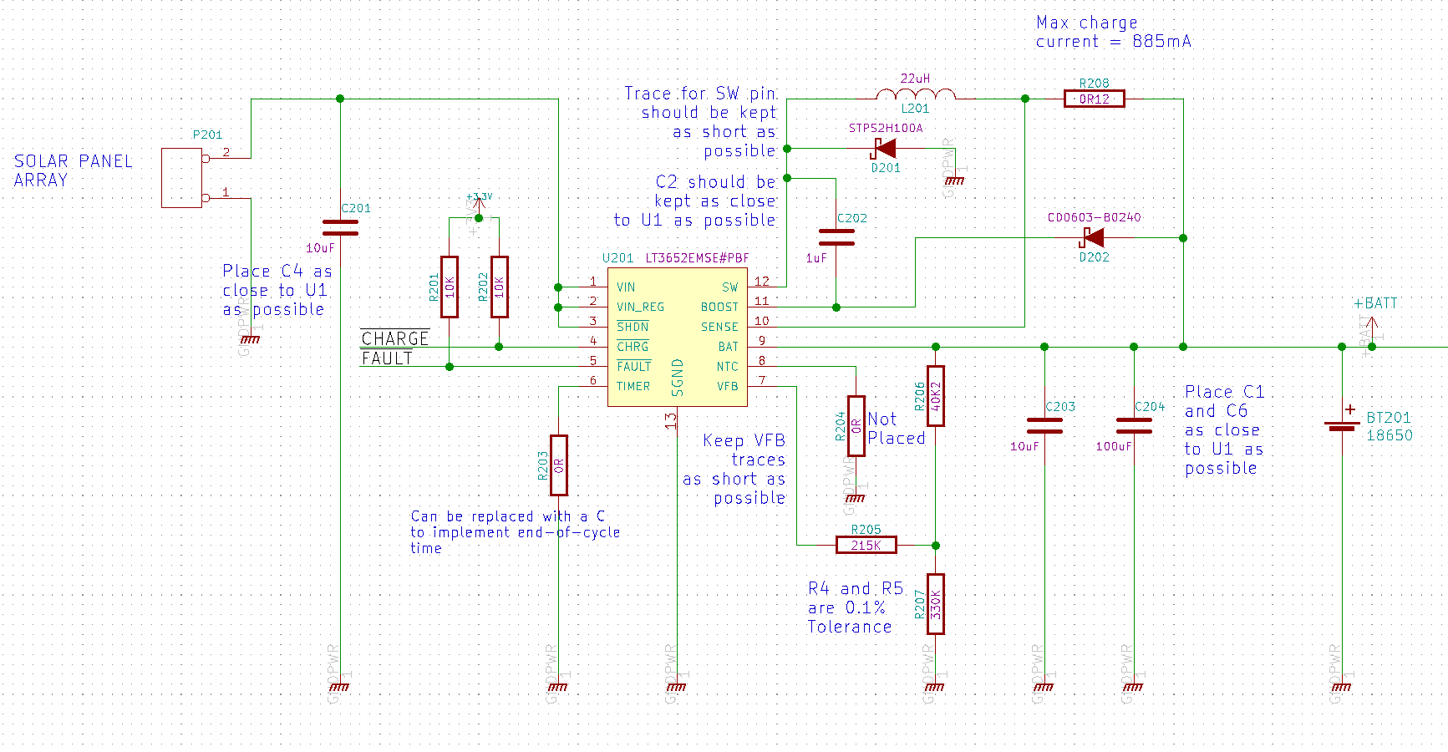
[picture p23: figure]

4.3.1 Maximum charge current
The lithium ion cell used can charge at 1C (2.6A, 9.62W). Given that the maximum power provided the solar cell array is approximately 1W, the designed maximum charging current is calculated as below:

I!"#$(&'()* = 1000
2.8V (mA)
= 357 (mA)
R208 is the R+,-+, resistor. It’s value is calculated as follows: R+,-+, = R208 = 0.1 I"#$(&'()

= 0.1
| 0.357 (Ω)
= 280 (mΩ)
Selecting from E24 series resistor values, a 1% tolerance 270mOhm resistor is used for R208. The actual
I"#$(&'() = .//01
/.345 = 370mA, however for simplicity, 357mA will be used for remaining calculations.
| Requirement | Solution
Resistance | 270mΩ | 270mΩ
Tolerance | 1% | 1%
Minimum current rating specification | 370mA + 50% margin = 555mA | 900mA

4.3.2 Input voltage supply decoupling capacitor
This is implemented using C201.
The manufacturer recommends using a high quality, low ESR decoupling capacitor at the input pin of LT3652. The decoupling capacitor is used to sink input ripple current. The input charging RMS ripple current I"16-(7&+) is given by the equation below.

I"16-(7&+) ≅ I"#$(&'() ∙

V8'9

V6- 5 V6-

V8'9

− 1 (A)

The above relation is maximum when V6- = 2 ∙ V8'9. We designed I"#$(&'() = 0.357A. Therefore:

I"16-(7&+) = I"#$(&'()
2
= 0.357
2 = 0.18 (A)

Therefore, the maximum input charging RMS input current I"16-(7&+) is 0.18A.
The minimum bulk capacitance required at the input is given by the below equation, where ΔV6- = 100 mV. This is the maximum acceptable ΔV6- as specified by the manufacturer.

C6-(8:;<) = I"#$(&'() ∙ 9 V8'9
V6- ∙ ΔV6-

: (μF)
= 0.18 ∙ 9 4.2
9 ∙ 0.1

: (μF)
= 0.84 (μF)
The voltage rating of C201 needs to have voltage rating greater than 9V (three solar cells in series) as well as maintain sufficient capacitance at the operating voltage such that the input ripple voltage is maintained below 100mV.
The manufacturer recommends a value of 10uF for C201. The below solution has been chosen.

Solution MPN | Requirement | AVX, TPSD106K035R0125
Capacitance | 10uF | 10uF
Tolerance | 10% | 10%
ESR | Low | 0.12mΩ
Voltage rating | 9V + 50% margin = 13.5V | 35V
Rated ripple current | 0.18A + 50% margin = 0.27A | 0.986A [at 85°C, 35V]

This solution will achieve an input charging RMS ripple voltage of:

ΔV6- = I"#$(&'() ∙ ? V8'9
V6- ∙ C6-(8:;<)

@

= 0.357A ∙ 9

4.2V
9 ∙ 10:
= 17 mV < 100 mV

4.3.3 Boost supply
The internal switch driver uses a bootstrapped power supply to drive the internal switch transistor. For correct start-up, the BOOST pin must be above 2V with respect to the SW pin (or VIN pin must be above 3.3V with respect to the SW pin). For correct operation, the VBOOST cannot exceed 8.5V with respect to the SW pin. C202 acts as the bootstrap capacitor. The value of 1uF is recommended by the manufacturer. The voltage rating of C202 must exceed the maximum BAT voltage of 4.2V.
A bootstrap diode D202 connected between the BAT pin and the BOOST pin is required to facilitate the bootstrapping mechanism. The manufacturer recommends using a diode with average current greater than 0.1A and a reverse voltage greater than V6-(&'() of 9V.
Solution MPN | Requirement | Bourns, CD0603-B0240
Forward voltage | Low | 0.55V (at IF= 0.2A)
Reverse voltage | 9V + 50% margin = 13.5V | 40V
Average forward current | 100mA + 50% margin = 150mA | 200mA
Reverse leakage current | Low | 10uA (at VR = 30V)

There is the option of using a Zener diode to clamp the voltage between BOOST and SW pins to be below 8.5V. However, this is not required as only one Li-ion cell is used where the BAT pin voltage will not exceed 4.2V.

4.3.4 MPPT temperature compensation
Temperature compensated MPPT (maximum power point tracking) can be implement using an LM234 3-terminal temperature sensor (U203) and resistor network R209, R210 and R203. The values for the resistors are calculated using the equations below.
R209 = −R203 ∙ (TC ∙ 4405)

R210 =
⎝

⎜

⎛ | R209

V&=(3>") + R209 ∙ G

0.0674
R203 I
V6-(7,$) | − 1

⎠

⎟

⎞

Where TC is the temperature coefficient (in V/°C) of the solar panel array. V&=(3>") is the maximum power voltage at 25°C.
For our 12 solar cell array, the specifications are:
TC = 0.07 (VC?.)
V&=(3>") = 9V
Let R203 = 1kΩ
R209 = −1kΩ ∙ (−0.078 ∙ 4405) = 344kΩ

R210 =
⎝

⎜

⎛ | 344kΩ

9V + 344k ∙ G

0.0674
1kΩ I
2.7V | − 1⎠

⎟

⎞ = 31.5kΩ

1% tolerance resistors were used for the resistor in this network. Selecting from E96 component values:
Resistor | Calculated value | Implemented value
R203 | 1kΩ | 1kΩ 1%
R209 | 344kΩ | 340kΩ 1%
R210 | 31.5kΩ | 31.6kΩ 1%

4.3.5 Output capacitor
Output decoupling capacitor C203 is required. The manufacturer’s recommended value is 10uF. The same capacitor used for C201 has been used for C203 to save on BOM count.

4.3.6 Inductor design
The primary criterion for inductor value selection in an LT3652 charger is the ripple current created in that inductor. Once the inductance value is determined, an inductor must also have a saturation current equal to or exceeding the maximum peak current in the inductor. An inductor value (L), given the desired amount of ripple current (ΔI&'() can be approximated using the relation:

L = 910 ∙

R+,-+,
ΔI&'(

: ∙ V8'9(@;9) ∙ ?1 − V8'9(@;9) V6-(&'()

@ (μH)

wℎere R+,-+, = R208
V8'9(@;9) = 4.2V
V6-(&'() = 9V
Where ΔI&'( is the normalised inductor ripple current. The manufacturer recommends setting ΔI&'( to between 25% and 35% of I"#$(&'(). We will set ΔI&'( to 30%. Therefore:

L = 910 ∙

0.28Ω

0.3 : ∙ 4.2V ∙ 91 − 4.2V
9V : (μH)
= 20.9 (μH)

The inductor also needs to meet the minimum volt-second requirement as specified in the equation below: volt second = V8'9(@;9) ∙ ?1 − V8'9(@;9)
V6-(&'()

@ (V. μs)

= 4.2V ∙ 91 − 4.2V
9V :
= 2.24 (V. μs)
Inductor maximum RMS and saturation current rations (I&'((7&+) and I+'9 respectively) are calculated as follows:

I+'9 = 91 +

ΔI&'(
2 : ∙ I"#$(&'()

= 91 +

0.3
2 : ∙ 0.357 (A)
= 0.41 (A)
I&'((7&+) > I"#$(&'()
> 0.357A
| Requirement | Murata, 46223C | TDK, SLF6025T-220MR73-PF
Inductance at 1MHz operating frequency | 22uH | 22uH | 22uH
Tolerance | 20% | 20% | 20%
DC resistance | Low | 120mΩ | 122mΩ (typ) 146.4mΩ (max)
Rated DC saturation current specification | 0.41A + 50% margin = 0.62A | 1.8A (defined when inductance falls below 75% or when component temperature reaches 40°C from TA=25°C). | 0.73A

4.3.7 Rectifier design
The rectifier diode from SW to GND, in a LT3652 battery charger provides a current path for the inductor current when the main power switch is disabled. The rectifier is selected based upon forward voltage, reverse voltage, and maximum current. A Schottky diode is required, as low forward voltage yields the lowest power loss and highest efficiency. The rectifier diode must be rated to withstand reverse voltages greater than the maximum VIN voltage. The minimum average diode current rating IA6BA,(&'() is calculated with maximum output current I"#$(&'(), maximum operational VIN, and output at the precondition threshold (V8'9(=7,) , or 0.7 ∙ V8'9(@;9)):

IA6BA,(&'() > I"#$(&'() ∙

V6-(&'() − V8'9(=7,)
V6-(&'()

(A)

IA6BA,(&'() > 0.357A ∙

9V − 0.7 ∙ 4.2V
9V (A)
IA6BA,(&'() > 0.24 (A)
Solution MPN | Requirement | ST Microelectronics, STPS2H100A
Forward voltage | Low | 0.6V typ. (at IF = 2A)
Reverse voltage specification | 9V + 50% margin = 13.5V | 100V (peak repetitive)
Average forward current | 0.24A + 50% margin = 0.36A | 2A
Reverse leakage current | Low | 1uA (at 25°C)

4.3.8 Battery float voltage programming
The float voltage of the battery is programmed using the resistor network R205, R206 and R207. V8'9(@;9) can be programmed up to 14.4V. Because the battery voltage is across the V8'9(@;9) programming resistor divider, this divider will draw a small amount of current from the battery at a rate of

I7@8 = 3.3
R207
Values for R205, R206 and R207 are calculated as follows R207

R206 = 3.3
V8'9(@;9) − 3.3
= 3.3
4.2 − 3.3 = 3.67

Setting I7@8 = 10μA yields: R207 = 3.3
10μA
R207 = 330kΩ

R206 = 330kΩ
3.67 = 90kΩ

The equivalent input resistance at the VFB pin needs to be 250kOhm to compensate for input bias current error. Therefore:
R205 = 250kΩ − 90kΩ = 160kΩ
Resistor | Calculated value | Implemented value
R205 | 160k | 160kΩ 1%
R206 | 90kΩ | 90.9kΩ 1%
R207 | 330kΩ | 330kΩ 1%

4.4 3V3 power supply
Power supply requirements
| Requirement | Solution
Minimum output current requirement | 0.794A | 1.6A (min, VIN = 3.6V, TA = 25°C)
Output voltage | 3.3V +/- 10%
Output voltage ripple | +/-300mV
Input voltage range | 2.8V to 4.2V | 1.8V to 5.5V
Efficiency | > 80% at 0.794A

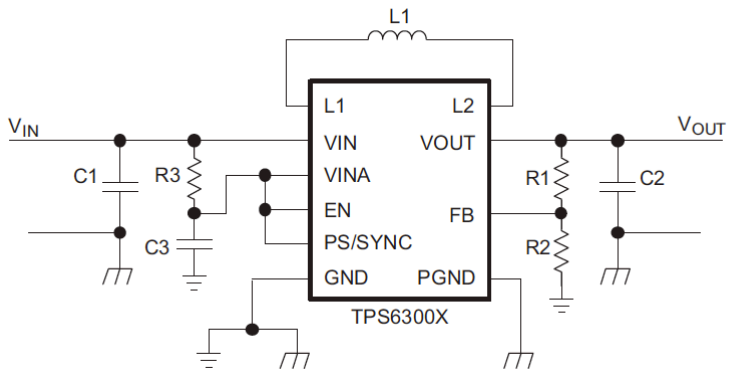
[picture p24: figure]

The TPS63001 voltage regulator (U202) is to switch mode buck-boost converter to efficiently convert the output voltage of the battery to 3V3.

4.4.1 Input capacitors
TPS63001 requires at least 4.7uF of input capacitance to improve transient behaviour of the regulator and EMI behaviour of the total power supply circuit. The input capacitor for this design is required to have a voltage rating greater than 4.2V. The reference design provided by the manufacturer uses a GRM188R60J106KME84D, 10uF capacitor from Murata. This is used in the instrumentation buoy logic board.

4.4.2 Output capacitors
TPS63001 requires at least 15uF of output capacitance. The reference design for TPS63001 has two 10uF capacitors at its output. The capacitor is required to have a voltage rating greater than 3.3V. The manufacturer recommends the GRM188R60J106KME84D from Murata for both output capacitors. This is used in the instrumentation buoy logic board.

4.4.3 Inductor design
L202 is the inductor for the buck-boost mechanism. The peak inductor current is calculated using the equations below:
D = VB:9 − V6-
VB:9

I=,'< = IB:9
η × (1 − D) +

V6- × D
2 × f × L
Where:
V6- | Minimum input voltage | 2.8V
VB:9 | Output voltage | 3.3V
η | Efficiency of the converter at worst case loading | 80%
f | Converter operating frequency | 1.25MHz to 1.8MHz
L | Inductance of inductor at operating frequency | 2.2uH

D = 3.3 − 2.8
3.3 = 0.15

I=,'< = 0.529 0.8 ∙ (1 − 0.15) +

2.8 ∙ 0.15
2 ∙ 1.25MHz ∙ 2.2μH
= 0.85A

The datasheet recommends using a 2.2uH inductor. The solution is listed below.
Solution MPN | Requirement | TDK, VLS3015CX-2R2M-1
Inductance at 2.4MHz operating frequency | 2.2uH | 2.2uH
Tolerance | 20% | 20%
DC resistance | Low | 64 mΩ(max)
Rated DC saturation current specification | 0.85 + 50% margin = 1.28A | 1.71A (30% drop in inductance)

4.4.4 Thermal design
The resistive heating P7 dissipated during operation at I=,'< is calculated below: P7 = I=,'<

3 ∙ RA"
= 0.85³ ∙ 0.087
= 63 (mW)
Calculating the ΔT between the IC junction and ambient at peak power. ΔTC' = 0.063 ∙ RDC'
= 0.063W ∙ 48.6°CW?.
= 3.1°C
At maximum ambient temperature of 30°C, the junction temperature will be 33.1°C. This is well below the maximum operating junction temperature of 125°C, therefore no heat sinking is required.
4.5 Layout considerations
The manufacturer recommends the below layout.

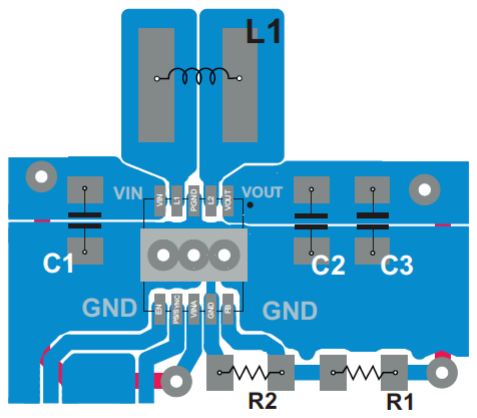
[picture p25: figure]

## 5 Microcontroller

5.1 RTC
The RTC is used to keep track of the time so that the data can be timestamped. Allowable drift of the RTC is 20mins per year.
The 32.768kHz crystal used was the CC4V-T1A 32.768KHZ +-20PPM 9PF. The specifications for the crystal are listed below:
Load capacitance C; | 9.0pF
Frequency tolerance | 30ppm
Drive power | 1.0uW
Aging first year max. | 3ppm
Frequency vs temperature | -0.035ppm/°C

A properly designed oscillator with this crystal will exhibit a theoretical maximum frequency drift of 30 + 3 + 0.7 = 33.7ppm after one year of operation. This equates to 18 mins per year.
Calculations of C309 and C310, the external capacitors for the crystal are as follows, assuming the stray capacitance between the crystal pins is 3pF.
C309 = C310 = 2 ∙ (C; − C+97'E) = 2 ∙ (9.0pF − 3.0pF)
= 12pF

5.2 HC-12
The HC-12 is the wireless module that allows UART communication to occur wirelessly. The effective range is 1km, given an adequate antenna.
5.3 Battery voltage measurement
The battery voltage is measured using a resistor divider R301 and R302. The values were chosen such that the voltage at +BAT_AD is 3V when the +BATT net is 4.2V. Schottky diode D301 with V@ < 200mV is used to clamp voltage at +BATT_AD to less than 3.5V to protect the MCU pin. The ADC reading this voltage is 10 bits. This gives a resolution of 3.2mV.
VF8'99 = 3.3V ∙ | 10kΩ 10kΩ + 4.7kΩ
+BATT voltage | +BATT_AD voltage | ADC count (10 bits, 0 to 1023)
2.8V | 1.90V | 589
4.2V | 2.86V | 887

## 6 Sensing

6.1 Accelerometer
The accelerometer used is the ADXL343. It is set to operate at the +/-2g range, 100Hz output data rate. The accelerometer requires a 1uF decoupling capacitor at the VS pin (C401) and a 100nF decoupling capacitor at the VDDIO pin (C402).

6.2 Pressure sensor
The pressure sensor ABPMANN005PG2D3 used is a digital pressure sensor with I2C interface. It is rated to 5 PSI, gauge pressure, DIP package with single axial barbed port.
The formula for translating counts to pressure is given below.

Where:

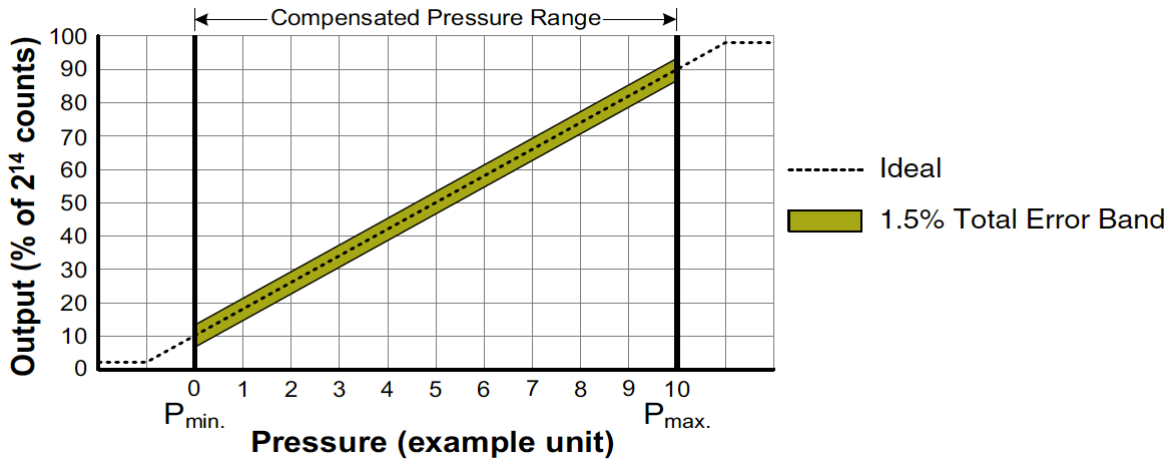
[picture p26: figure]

Output (% of 2.Gcounts) = 80%
P0HI − P0JK
- kPHLLMJNO − P0JKl + 10%
wℎere P0JK = 0 PSI, P0HI = 5 PSI 6.3 Depth measurement
The depth measurement apparatus is used to measure the depth that the buoy is submerged in the water as it floats in the ocean. It does this using an using two 800mm metal rods made from nichrome with a resistivity ρPQO of 13.77Ω/m, strapped on the side of the buoy. A schematic of the apparatus is shown in Figure 1 where x is the water depth as measured from the top of the buoy. The resistance RA,=9# measured between points a and b is given by the expression below. The resistivity of seawater ρRNHSHTNP = 0.2Ωm?..
RA,=9# = 2 ∙ ρPQOx + ρRNHSHTNP ∙ 0.314 = 27.54x + 0.0628 Ω

RA,=9# is driven by a constant current source built around D401, R402, R404 and Q402. The design of the current source is outlined below.

6.3.1 Zener diode design
The current source will be designed to source 30mA of current. 30mA is a good trade-off between signal to noise ratio and power consumption.
A 1.8V Zener diode was selected as the voltage reference. To maintain a 1.8V Zener voltage, the Zener voltage needs to be around 600uA. This current is programmed using R402.
R402 = 3.3V − 1.8
0.6mA = 2.5kΩ

The implemented value for R402 is 2.4kΩ, selected from E24 values.
The transistor Q402, when switched on exhibits a V8, of 0.70V. There the emitter current I, and base current I8 of Q402 is
I, = 1.8V − 0.7V
R404 | =
I8 = | I,

ℎ@, + 1 = 1.8V − 0.7V
R404 ∙ (ℎ@, + 1)

The current of the current source equals the collector current of Q402. Therefore, the current source current is calculate as follows:
I" = I, ∙ ℎ@,

ℎ@, + 1 = (1.8V − 0.7V) ∙ ℎ@, R404 ∙ (ℎ@, + 1)
R404 = (1.8V − 0.7V) ∙ ℎ@,
I" ∙ (ℎ@, + 1) = 36Ω

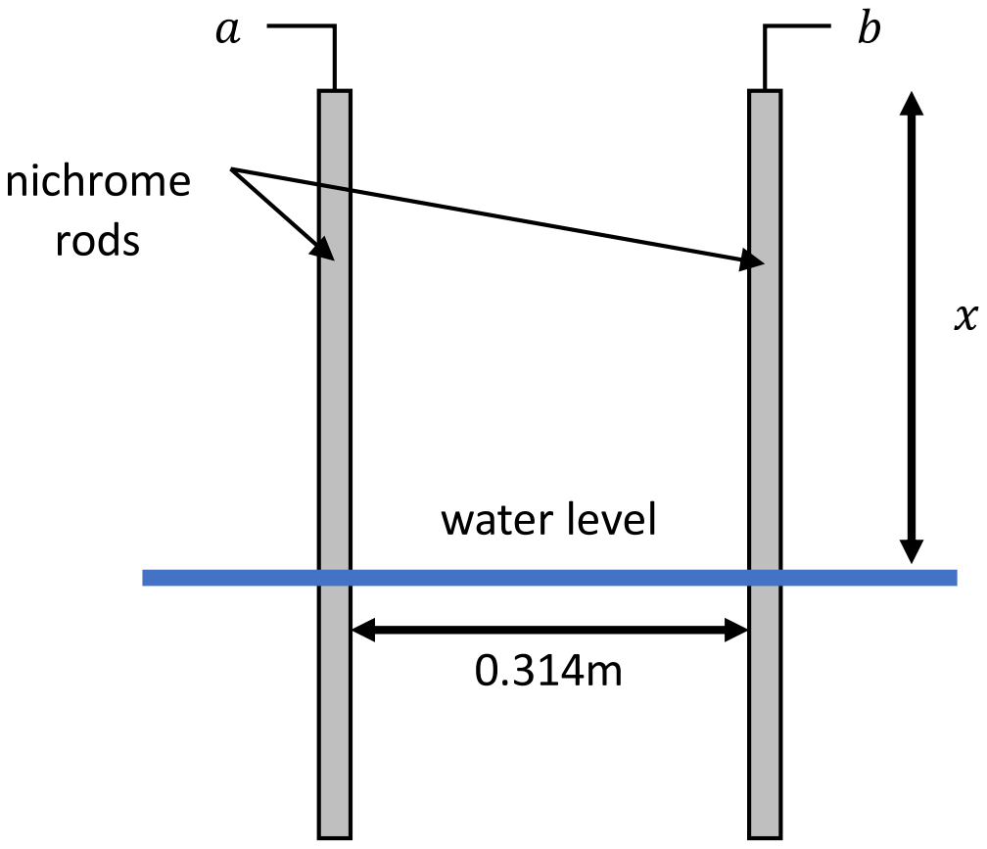
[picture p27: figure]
water level; nichrome rods

Figure 1
6.3.1 Instrumentation amplifier
We would like to resolve the depth to within 5mm over 800mm (0.6%). We calculate the minimum and maximum values of RA,=9#.
RA,=9#(&6-) = 27.54 ∙ 0 + 0.0628 Ω = 0.0628Ω
RA,=9#(&'() = 27.54 ∙ 0.8 + 0.0628Ω
= 22.1Ω
The voltage across RA,=9# is as follows VA,=9#(x) = (27.54 ∙ x + 0.0628) ∙ 0.03 (V) VA,=9#(&6-) = 0.0628 ∙ 30mA = 1.88mV VA,=9#(&'() = 22.1 ∙ 30mA = 663mV To amplifier the signals such that VA,=9#(&'() is amplified to 3.0V, the gain of the instrumentation amplifier needs to be around 4.52. The gain of the instrumentation amplifier can be calculated as below.
G = VB:9
VH − VU

= 1 +

R.
R3

+

2R.
R$
= 4.60
Where
R. = RN401A = RN401D = 56kΩ R3 = RN401B = RN401C = 56kΩ R$ = R407 = 43kΩ
The output voltage to the ADC is as follows V'A" = 4.60 ∙ (27.54 ∙ x + 0.0628) ∙ 0.03 = 0.138 ∙ (27.54 ∙ x + 0.0628)

The ADC count (10 bit ADC) is calculated as follows

COUNT'A" = 1023 ∙

V'A"
3.3 = 42.78 ∙ (27.54x + 0.068)

= 1178x + 2.91

x = (COUNT'A" − 2.91)
1178 | (m)

Where x is the water depth as measured from the top of the buoy.
The signal is passed through a low pass filter implemented with R409 and C403 with a cut-off frequency of 1kHz to attenuate noise before being fed into the ADC of the microcontroller.

## 7 LED drive

7.1 Light detect
A photoresistor (connected to P502) in conjunction with a resistor R510 is used to detect night and day and automatically used to switch on the LED lights. The VT90N1 has a resistance between 6kΩ and 18kΩ at 10 lux and 200k at 0 lux. The signal is fed through a low pass filter before being fed into the ADC pin. The specifications for the light detect circuit is shown below.
| 10 lux | 0 lux
Min voltage / ADC count at LIGHT_DETECT_AD | 2.50V / 755 | 0.72V / 223
Max voltage / ADC count at LIGHT_DETECT_AD | 2.99V / 927 | 0.72V / 223

7.2 LED
The buoy uses six Cree Inc. CLA2A-WKW-CYBZ0343 white LED modules (LED501 to LED506). Each LED module contains two LEDs. The LEDs have the following specifications:
Colour temperature | 5500K typ.
Luminous intensity (at IF = 2 x 20mA) | 3550 to 5600 mcd
Forward current | 2 x 25mA
Peak forward current | 2 x 100mA (pulse width =< 0.1s, duty =< 0.1)
Forward voltage (at IF = 20mA) | 3.2V typ., 4.0V max
Viewing angle | 60 degrees (when relative luminous intensity drops by 50%)

The LEDs have been designed to operate at 20mA per diode which achieves a relative luminous intensity of 1. The buoy will shine with a luminous intensity between 21.3cd and 33.6cd per flash.
7.3 LED driver
The FAN5333A from ON Semiconductor (U501) was selected to drive the LED array. The specifications for FAN5333A are shown below:
Requirement | Specification

Input voltage range | 2.8V to 4.2V | 1.8V to 5.5V
Output voltage | Greater than 19.5V | From VIN to 30V
Output load current | Greater than 40mA | 65mA min.

7.3.1 Maximum output voltage
The output voltage is calculated to ensure that the voltage is within the capabilities of the FAN5333A chip. VB:9 = V@8 + VA + 6 ∙ V;,A
= 0.11V + 0.18V + 6 ∙ 3.2V = 19.49V ≅ 19.5V The calculated output voltage is within the maximum output voltage capability of the FAN5333A.

7.3.2 Setting output current
The output current is programmed by selecting the feedback resistor R512. For the FAN5333A, V@8 = 0.11V. R512 = V@8
I;,A

= 0.11V
20mA = 5.5Ω

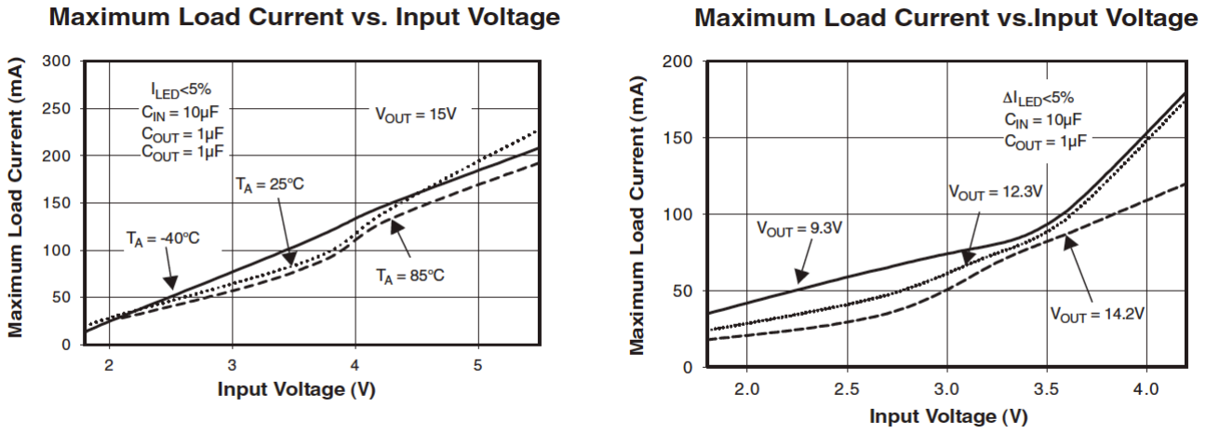
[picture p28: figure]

Examining the current and voltage curves of the FAN5333A, the required output current of 40mA can only be maintained if the battery voltage is above 3.0V. This is sufficient as the battery voltage will likely be high at the start of evening due to an entire day of charging under the sun. If the 40mA output current cannot be sourced, the LEDs will still be able to shine with sufficient brightness.

7.3.3 Inductor design
The manufacturer recommends using a 10uH inductor with saturation current greater than 1A and a DC resistance as low as possible to improve converter efficiency. The SLF6025T-100M1R0-PF from TDK was selected, which is also a part recommended by the manufacturer.
| Requirement | TDK, SLF6025T-100M1R0-PF
Inductance | 10uH | 10uH
DC resistance | Low | 68.76mΩ (max)
Saturation current | Equal or greater than 1A | 1A

7.3.4 Capacitor selection
The manufacturer recommends input and output capacitors of values 10uF and 1uF respectively. These are implemented by capacitors C505 and C501 respectively, X5R SMD ceramic capacitors.

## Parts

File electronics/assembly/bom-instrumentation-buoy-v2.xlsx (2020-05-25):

Reference | Internal Part Number | Quantity | Component Value | Manufacturer | Manufacturer Part Number | Part Description
BT201 | ECS00215 | 1 | 3.7V | SparkFun Electronics | PRT-13189 | BATTERY LITHIUM 3.7V 2.6AH
C202 C301 C308 C401 C501 | ECS00052 | 5 | 1uF | Murata | GRM188R61H105KAALD | 1uF, 0603, 10%, 50V, X5R, Ceramic
C203 C201 | ECS00053 | 2 | 10uF | AVX | TPSD106K035R0125 | 10uF, 2917, 10%, 35V, Tantalum
C205 C208 C207 | ECS00050 | 3 | 10uF | Murata | GRM21BR61A106KE19L | 10uF, 0805, 10%, 10V, X5R, Ceramic
C206 C303 C302 C304 C306 C305 C403 C402 C504 | ECS00075 | 9 | 100nF | Murata | GRM188R71C104KA01D | 100nF, 0603, 10%, 16V, X7R, Ceramic
C307 | ECS00078 | 1 | 220nF | Murata | GRM188R71A224KA01D | 220nF, 0603, 10%, 10V, X7R, Ceramic
C309 C310 | ECS00204 | 2 | 12pF | Murata | GCM1885C2A120FA16D | 12pF ¬±1% 100V Ceramic Capacitor C0G, NP0 0603 (1608 Metric)
C505 | ECS00051 | 1 | 10uF | Murata | GRM31CR61H106KA12L | 10uF, 1206, 10%, 50V, X5R, Ceramic
D201 | ECS00095 | 1 |  | ST Microelectronics | STPS2H100A | Schottky, Single, 2A, SMD
D202 D301 D502 | ECS00037 | 3 |  | Bourns | CD0603-B0240 | Schottky, Single, 0.1A, SMD
D401 | ECS00072 | 1 | 1.8V | On Semiconductor | MMSZ4678T1G | Zener, 1.8V, 0.25W, SMD
J301 | ECS00065 | 1 |  | Amphenol Commercial Products | 114-00841-68 | Micro SD Card Holder, SMD
L201 | ECS00071 | 1 | 22uH | Murata | 46223C | 22uH, 1.8A, 0R12
L202 L501 | ECS00210 | 2 | 2.2uH | TDK | VLS3015CX-2R2M-1 | IND PWR CIR WOUND FERRITE MATERI
L401 | ECS00074 | 1 | 1kK @ 100MHz | Murata | BLM18TG102TN1D | 1K @ 100MHz, 0603, 0.1A, 0R6
LED301 LED302 | ECS00035 | 2 | Red | Rohm | SML-310VTT86L | Red, 4mcd, 0603
LED501 LED503 LED505 LED506 LED502 LED504 | ECS00208 | 6 | White | Cree Inc. | CLA2A-WKW-CYBZ0343TR-ND | LED COOL WHITE DIFF 4PLCC SMD
P201 P502 | ECS00004 | 2 | 2x1 | Molex | 22-28-4020 | 2-way, header, 2.54mm pitch, vertical, through hole, KK Series
P401 | ECS00067 | 1 | 2x1 | JST | B2B-PH-SM4-TB(LF)(SN) | 2-way, header, 2mm pitch, vertical, SMD, PH Series
Q401 | ECS00087 | 1 |  | On Semiconductor | NTA4153NT1G | MOSFET, N-Channel, 0.915A, 0R127
Q402 | ECS00073 | 1 |  | NXP | BC857BW,115 | BJT, PNP, 45V, 0.1A
R202 R201 R302 R305 R306 R401 R502 | ECS00045 | 7 | 10K | Panasonic | ERJ3GEYJ103V | 10K, 0603, 5%, 0.1W, Thick Film
R203 | ECS00049 | 1 | 1K | Panasonic | ERJ3EKF1001V | 1K, 0603, 1%, 0.1W, Thick Film
R204 | ECS00200 | 1 | 100R | Panasonic | ERJ-3EKF1000V | 100 Ohms ¬±1% 0.1W, 1/10W Chip Resistor 0603 (1608 Metric) Automotive AEC-Q200 Thick Film
R205 | ECS00119 | 1 | 160K | Panasonic | ERJ-3EKF1603V | 160 kOhms ¬±1% 0.1W, 1/10W Chip Resistor 0603 (1608 Metric) Automotive AEC-Q200 Thick Film
R206 | ECS00118 | 1 | 90.9K | Panasonic | ERJ-3EKF9092V | 90.9 kOhms ¬±1% 0.1W, 1/10W Chip Resistor 0603 (1608 Metric) Automotive AEC-Q200 Thick Film
R207 | ECS00047 | 1 | 330K | Panasonic | ERJ3EKF3303V | 330K, 0603, 1%, 0.1W, Thick Film
R208 | ECS00115 | 1 | 0R27 | Bourns | CRL1206-FW-R270ELF | RES 0.27 OHM 1% 1/4W 1206
R209 | ECS00116 | 1 | 340K | Panasonic | ERJ-3EKF3403V | 340 kOhms ¬±1% 0.1W, 1/10W Chip Resistor 0603 (1608 Metric) Automotive AEC-Q200 Thick Film
R210 | ECS00117 | 1 | 31.6K | Panasonic | ERJ-3EKF3162V | RES SMD 31.6K OHM 1% 1/10W 0603
R301 R309 | ECS00086 | 2 | 4K7 | Bourns | CR0603-FX-4701ELF | 4K7, 0603, 1%, 0.063W, Thick Film
R303 R304 | ECS00081 | 2 | 68R | Bourns | CR0603-FX-68R0ELF | 68R, 0603, 1%, 0.1W, Thick Film
R308 R307 | ECS00084 | 2 | 2K2 | Multicomp | MC0063W060312K2 | 2K2, 0603, 1%, 0.063W, Thick Film
R402 | ECS00201 | 1 | 2.4K | Panasonic | ERJ-3EKF2401V | RES SMD 2.4K OHM 1% 1/10W 0603
R404 R403 | ECS00080 | 2 | 36R | Vishay | CRCW060336R0FKEA | 36R, 0603, 0.1W, Thick Film
R407 | ECS00203 | 1 | 43K | Panasonic | ERJ-3EKF4302V | RES SMD 43K OHM 1% 1/10W 0603
R409 R511 | ECS00083 | 2 | 1K5 | Bourns | CR0603-FX-1501ELF | 1K5, 0603, 1%, 0.1W, Thick Film
R510 | ECS00085 | 1 | 56K | Vishay | CRCW060356K0FKEAHP | 56K, 0603, 1%, 0.25W, Thick Film, High Power
R512 R501 | ECS00213 | 2 | 5.6R | Panasonic | ERJ-3RQF5R6V | RES SMD 5.6 OHM 1% 1/10W 0603
RN401 | ECS00206 | 1 | 56K | Yageo | TC164-FR-0756KL | RES ARRAY 4 RES 56K OHM 1206
U201 | ECS00043 | 1 |  | Linear Technology | LT3652EMSE#PBF | Switch Mode Charge Controller with MPPT
U202 | ECS00214 | 1 |  | Texas Instruments | TPS63001DRCR | IC REG BCK BST 3.3V 1.6A 10VSON
U203 | ECS00212 | 1 |  | ST Microelectronics | LM234DT | IC CURRENT SOURCE 3% 8SOIC
U301 | ECS00017 | 1 |  | Atmel | ATMEGA328P-AU | ATMega328P, TQFP
U302 | ECS00032 | 1 |  | Texas Instruments | BQ32000DR | RTC, 8SOIC
U303 | ECA00003 | 1 |  | HC | HC-12 | HC-12 Wireless UART Serial Data Module
U401 | ECS00114 | 1 | 5PSI | Honeywell | ABPDANN005PG2A3 | Pressure Sensor, Amplified, 5 psi, Digital, Gauge, 3.3 VDC, Single Axial Barbed, 3.1 mA
U402 | ECS00016 | 1 |  | Analog Device | ADXL343BCCZ | Accelerometer, 3 axis
U403 | ECS00030 | 1 |  | Microchip | MCP6042-E/MS | Dual Package, 8-MSOP, Unity Gain Stable
U501 | ECS00207 | 1 |  | ON Semiconductor | FAN5333BSX | IC LED DRIVER RGLTR DIM SOT23-5
X301 | ECS00005 | 1 | 32.768kHz | Micro Crystal Switzerland | CC4V-T1A 32.768KHZ +-20PPM 9PF | Crystal, 32.768kHz, 20ppm, 9pF, SMD

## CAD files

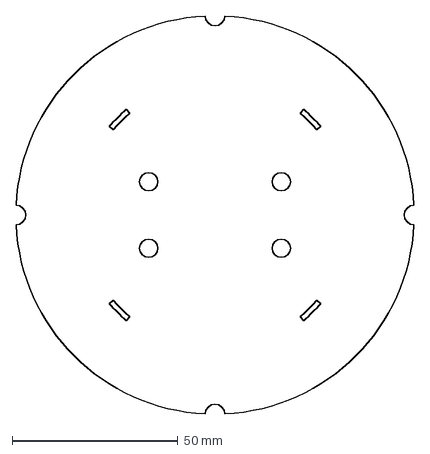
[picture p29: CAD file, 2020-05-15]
electronics/board_outline.dxf
119.9 x 119.9 mm

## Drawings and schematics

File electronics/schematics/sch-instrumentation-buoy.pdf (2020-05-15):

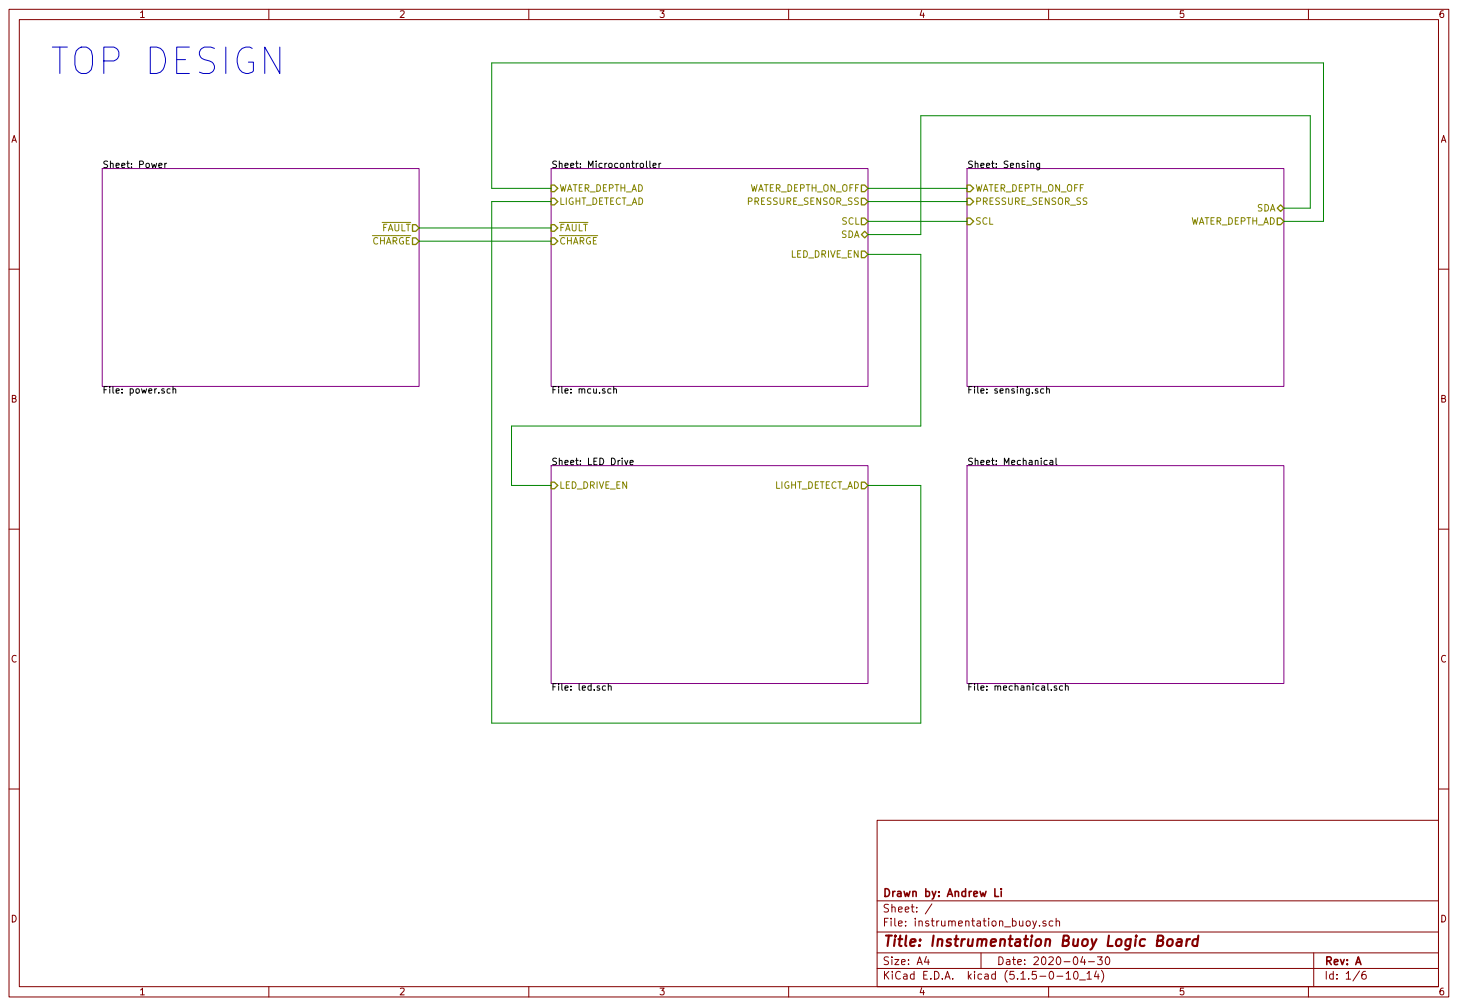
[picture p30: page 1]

Sheet: Mechanical File: mechanical.sch TOP DESIGN

Sheet: Microcontroller File: mcu.sch WATER_DEPTH_AD

Sheet: LED Drive File: led.sch

File: instrumentation_buoy.sch Sheet: / Drawn by: Andrew Li

Id: 1/6 Title: Instrumentation Buoy Logic Board

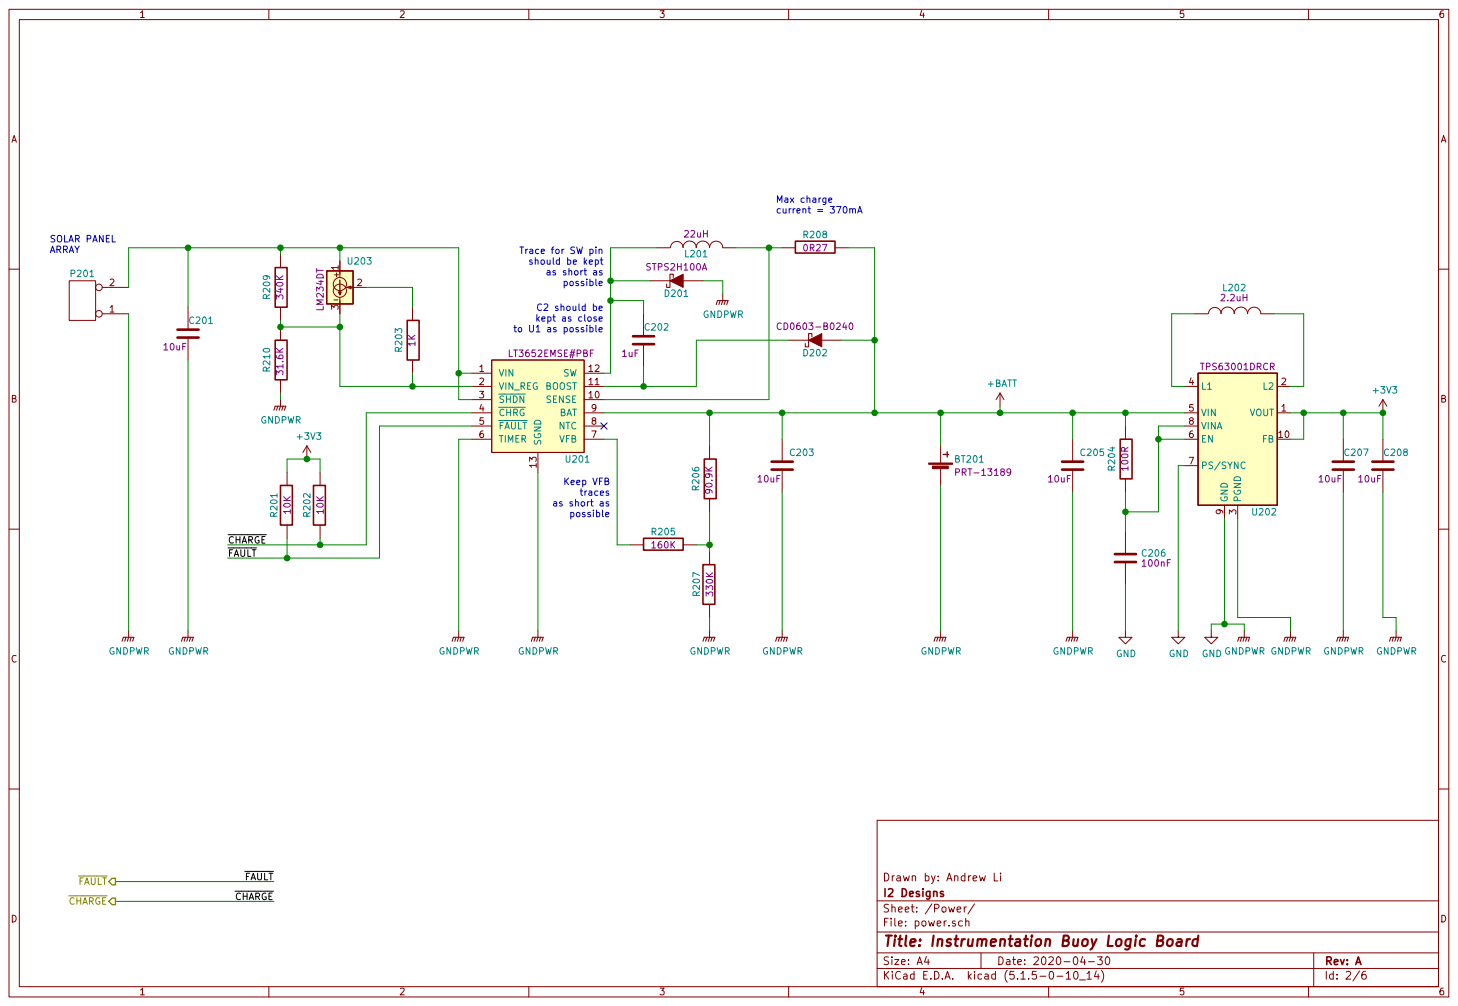
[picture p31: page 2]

traces as short as possible SOLAR PANEL ARRAY

Trace for SW pin
should be kept as short as possible C2 should be

Drawn by: Andrew Li
I2 Designs
File: power.sch Sheet: /Power/
Id: 2/6 Title: Instrumentation Buoy Logic Board

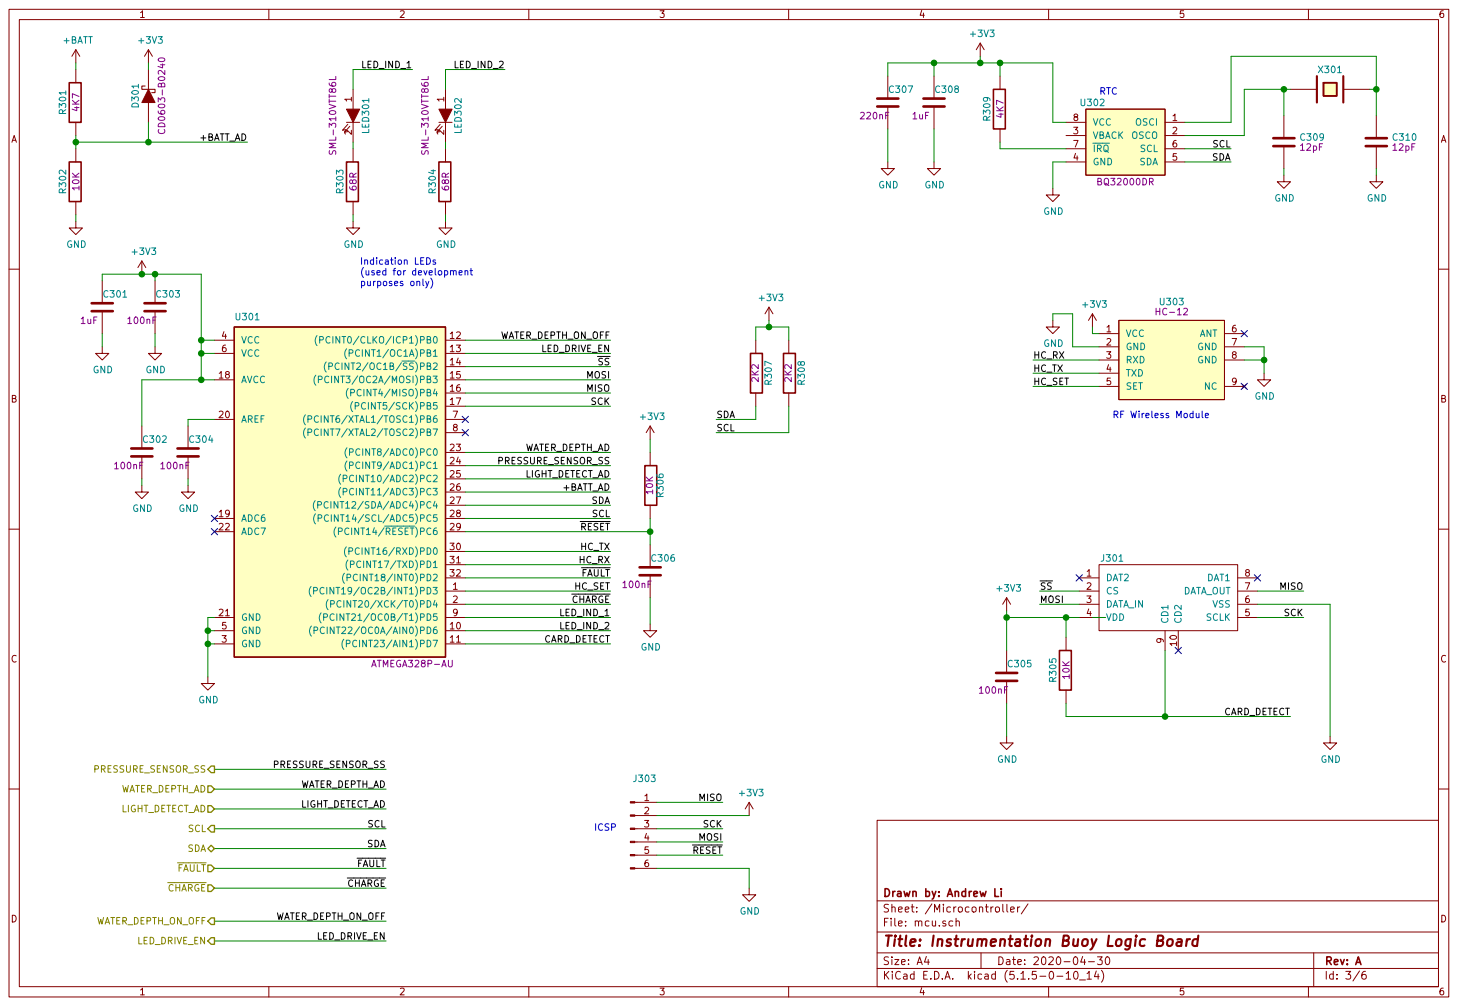
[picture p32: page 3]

SCL SDA WATER_DEPTH_ON_OFF SCL SDA HC_TX HC_RX
CHARGE MISO

Id: 3/6 Title: Instrumentation Buoy Logic Board

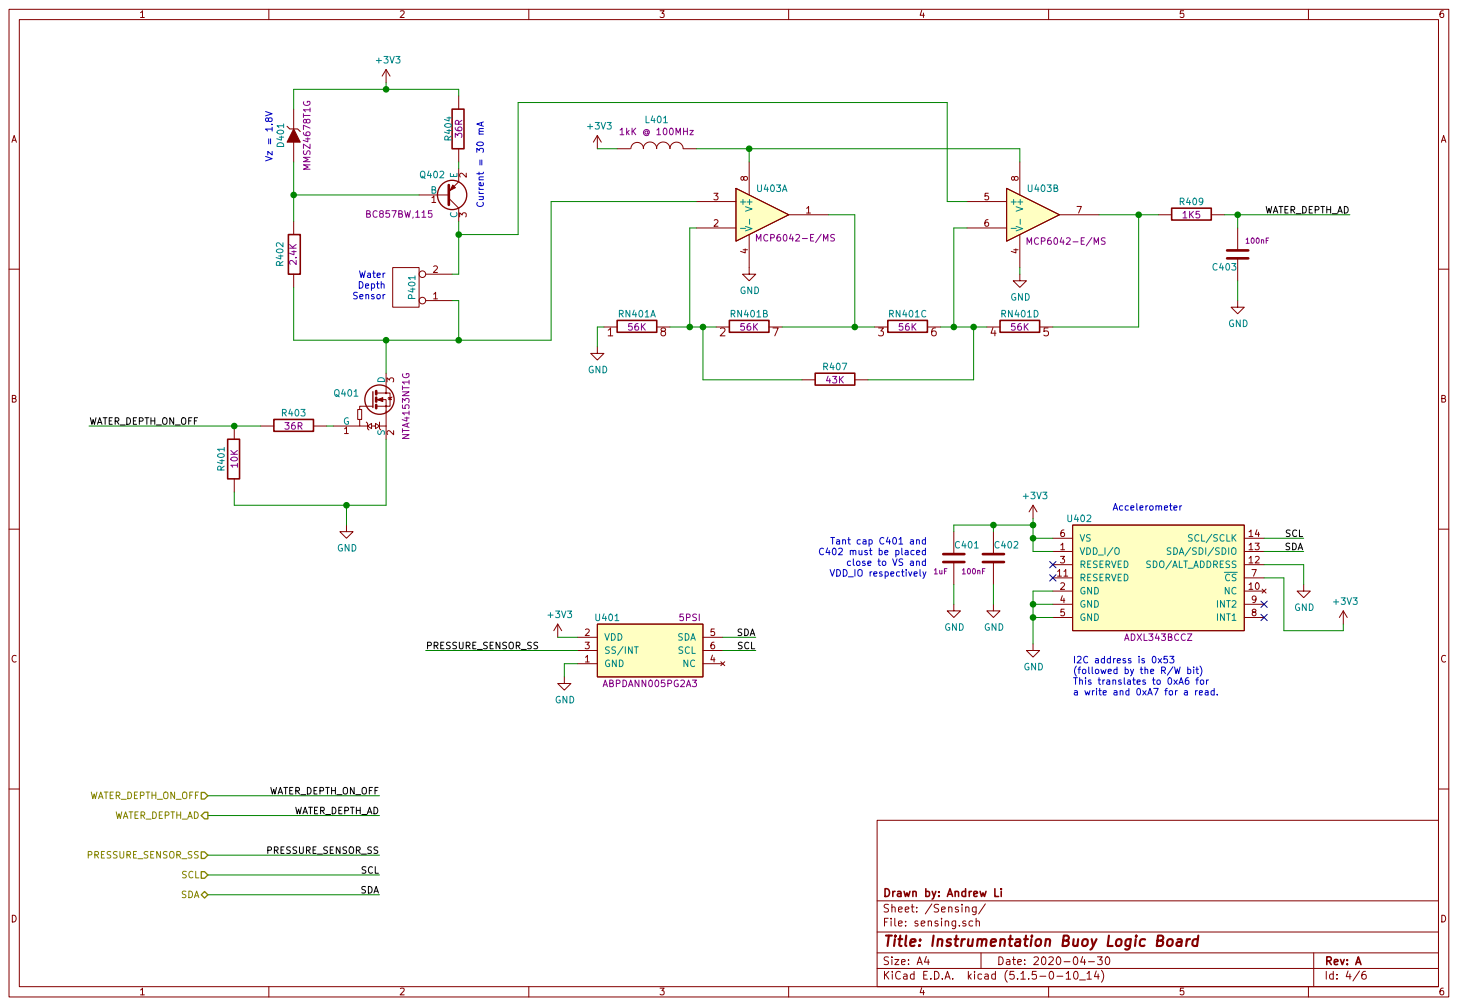
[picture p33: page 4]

close to VS and VDD_IO respectively Water Depth Sensor

I2C address is 0x53
(followed by the R/W bit) This translates to 0xA6 for a write and 0xA7 for a read.

Drawn by: Andrew Li
Sheet: /Sensing/
File: sensing.sch
Id: 4/6 Title: Instrumentation Buoy Logic Board

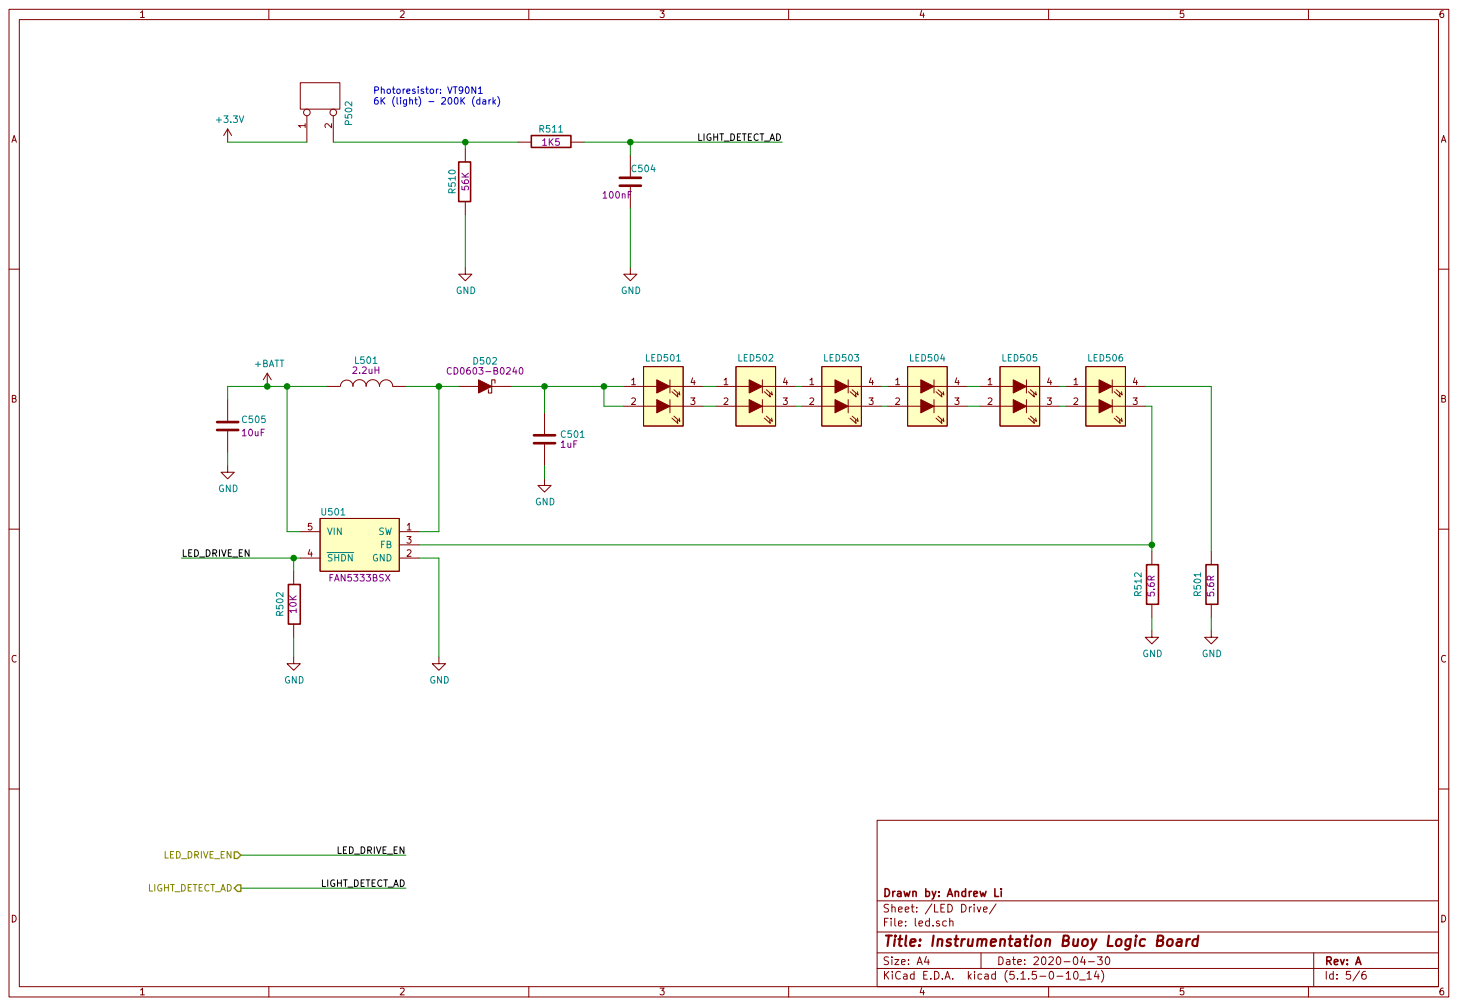
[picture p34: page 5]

File: led.sch Sheet: /LED Drive/ Drawn by: Andrew Li

Id: 5/6 Title: Instrumentation Buoy Logic Board

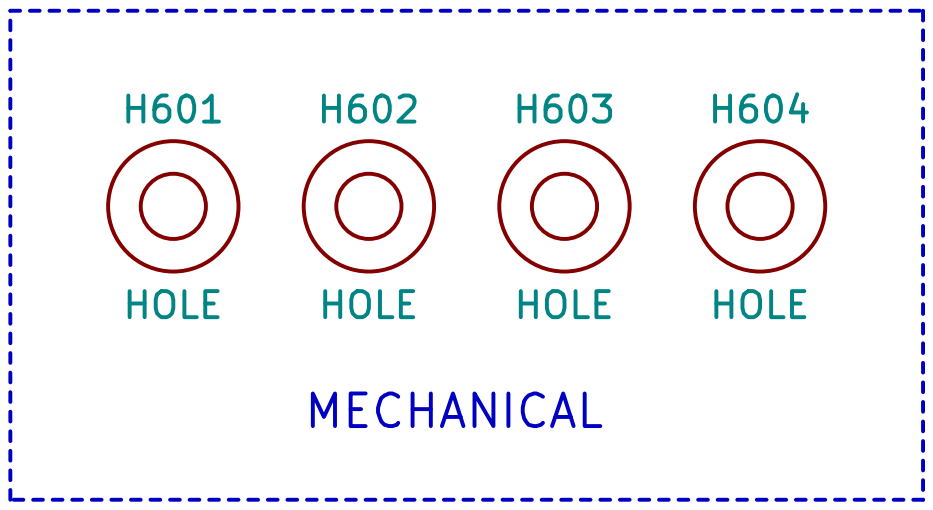
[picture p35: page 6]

File: mechanical.sch Sheet: /Mechanical/ Drawn by: Andrew Li

Id: 6/6 Title: Instrumentation Buoy Logic Board

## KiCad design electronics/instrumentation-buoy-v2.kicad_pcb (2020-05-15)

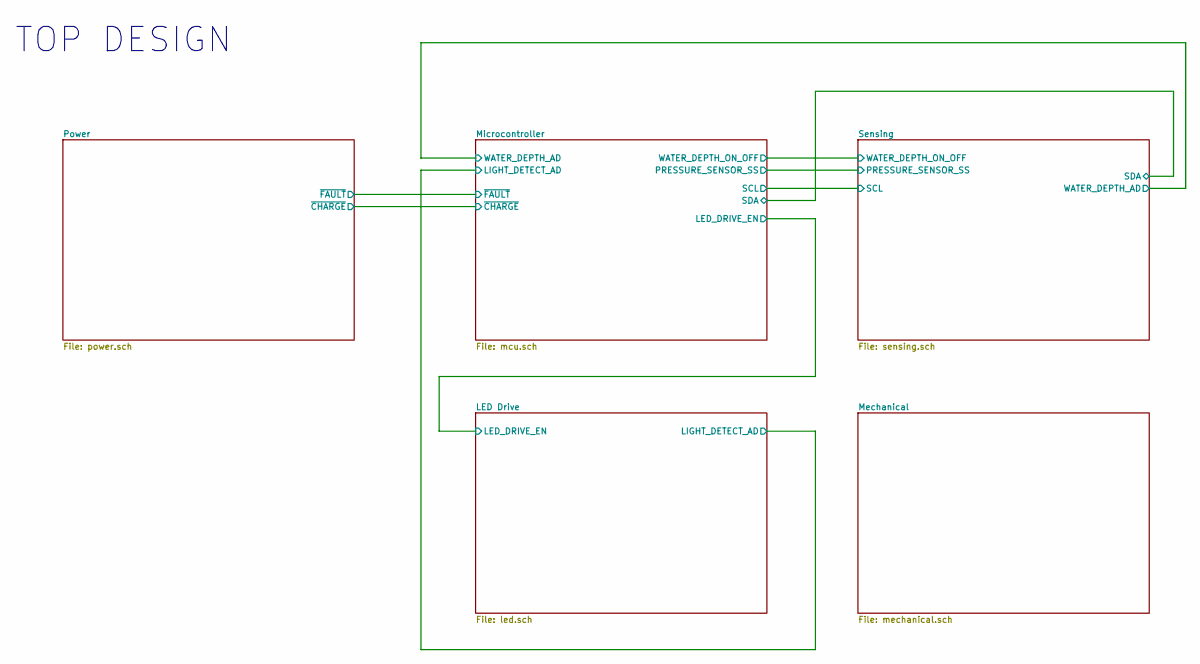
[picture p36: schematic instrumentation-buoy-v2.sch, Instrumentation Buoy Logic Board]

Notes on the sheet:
TOP DESIGN

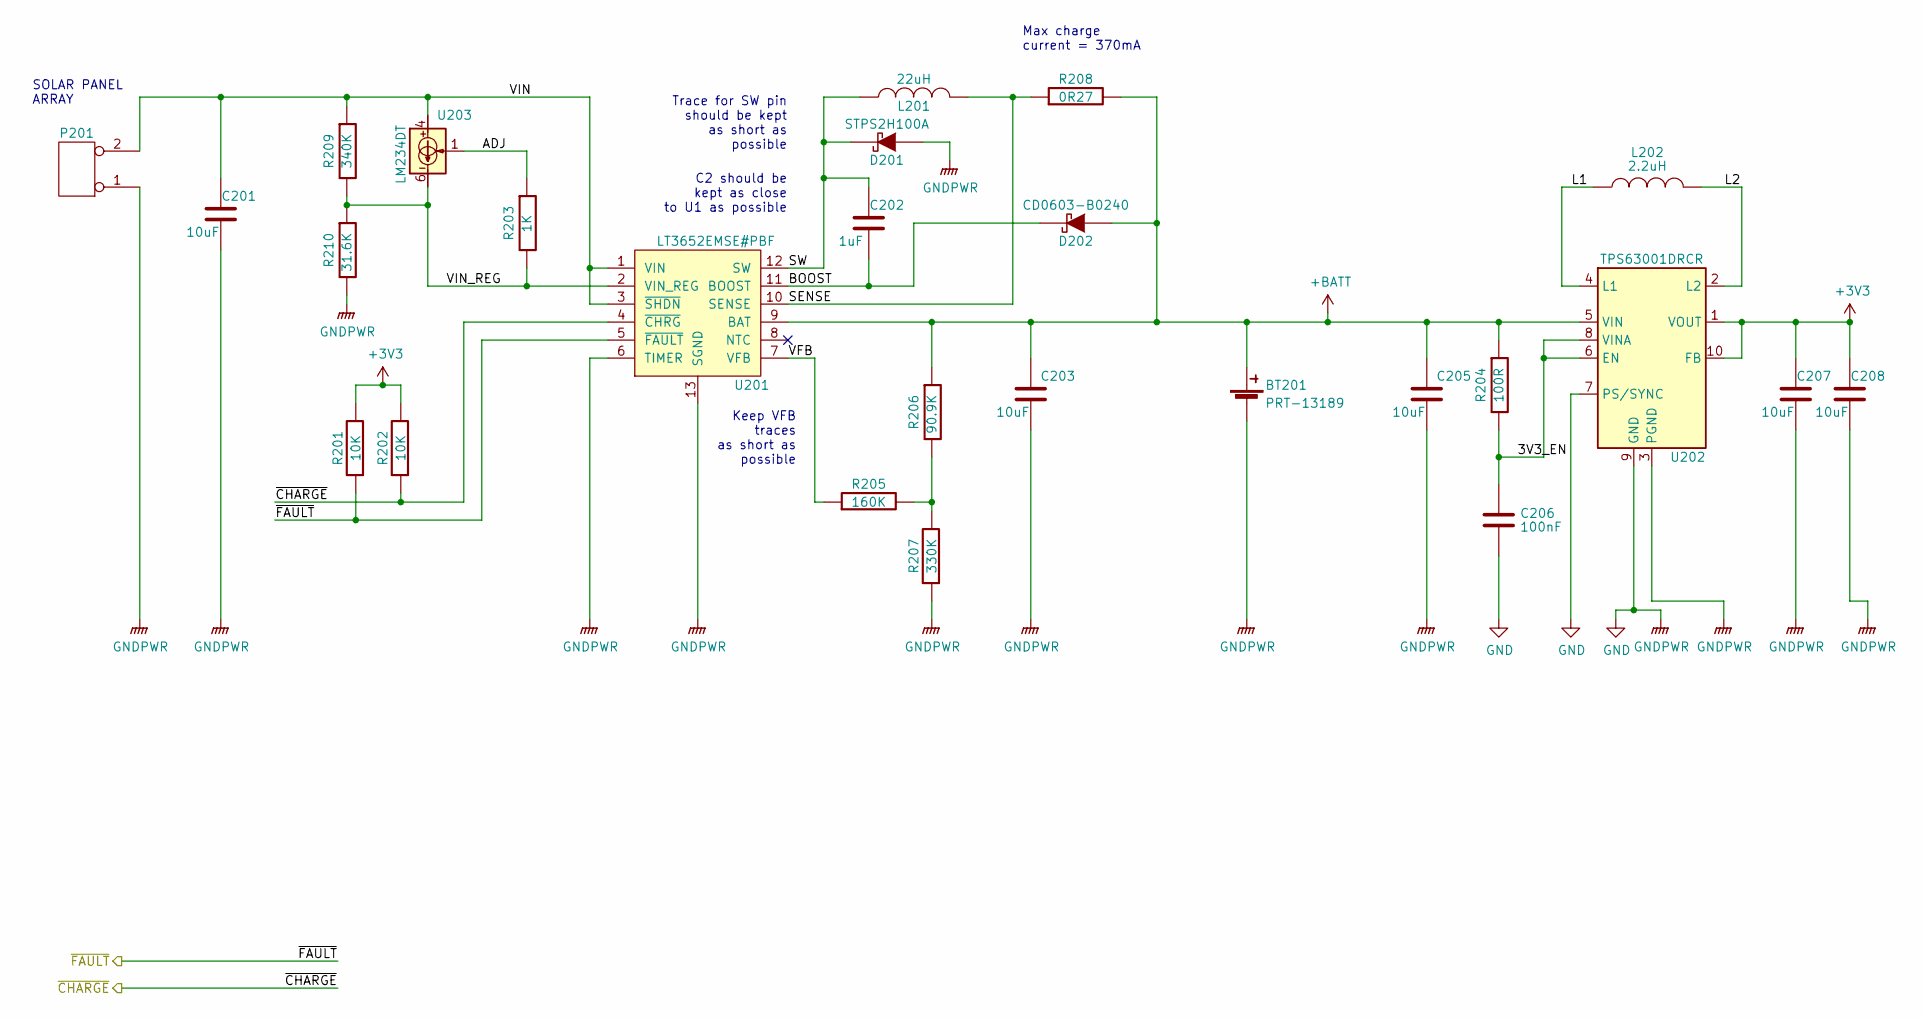
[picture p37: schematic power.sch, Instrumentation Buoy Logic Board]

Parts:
BT201: ECS00215; EC18650; Manufacturer Part Number PRT-13189
C201, C203: ECS00053; EC2917; Manfacturer Part Number TPSD106K035R0125
C202: ECS00052; EC0603_C; Manfacturer Part Number GRM188R61H105KAALD
C205, C207, C208: ECS00050; EC0805; Manfacturer Part Number GRM21BR61A106KE19L
C206: ECS00075; EC0603_C; Manfacturer Part Number GRM188R71C104KA01D
D201: ECS00095; ECDO-214AC(SMA); Manufacturer Part Number STPS2H100A
D202: ECS00037; EC0603_DIODE; Manufacturer Part Number CD0603-B0240
L201: ECS00071; ECS00071F; Manufacturer Part Number 46223C
L202: ECS00210; VLS3015CX-2R2M-1; Manufacturer Part Number VLS3015CX-2R2M-1
P201: ECS00004; ECS00004F; Manufacturer Part Number 22-28-4020
R201, R202: ECS00045; EC0603; Manufacturer Part Number ERJ3GEYJ103V
R203: ECS00049; EC0603; Manufacturer Part Number ERJ3EKF1001V
R204: ECS00200; EC0603; Manufacturer Part Number ERJ-3EKF1000V
R205: ECS00119; EC0603; Manufacturer Part Number ERJ-3EKF1603V
R206: ECS00118; EC0603; Manufacturer Part Number ERJ-3EKF9092V
R207: ECS00047; EC0603; Manufacturer Part Number ERJ3EKF3303V
R208: ECS00115; EC1206; Manufacturer Part Number CRL1206-FW-R270ELF
R209: ECS00116; EC0603; Manufacturer Part Number ERJ-3EKF3403V
R210: ECS00117; EC0603; Manufacturer Part Number ERJ-3EKF3162V
U201: ECS00043; ECMSOP-12D; Manufacturer Part Number LT3652EMSE#PBF
U202: ECS00214; Texas_DRC0010J_ThermalVias; Manufacturer Part Number TPS63001DRCR
U203: ECS00212; SOIC127P600X175-8N; Manufacturer Part Number LM234DT

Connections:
+BATT: BT201.1 (+), C203.1, C205.1, D202.1 (A), R204.1, R206.1, R208.2, U201.9 (BAT), U202.5 (VIN); also elsewhere on the board
/Microcontroller/~CHARGE: R202.1, U201.4 (~CHRG); also elsewhere on the board
/Microcontroller/~FAULT: R201.1, U201.5 (~FAULT); also elsewhere on the board
/Power/3V3_EN: C206.1, R204.2, U202.6 (EN), U202.8 (VINA)
/Power/ADJ: R203.1, U203.1
/Power/BOOST: C202.2, D202.2 (K), U201.11 (BOOST)
/Power/L1: L202.1, U202.4 (L1)
/Power/L2: L202.2, U202.2 (L2)
/Power/SENSE: L201.2, R208.1, U201.10 (SENSE)
/Power/SW: C202.1, D201.2 (K), L201.1, U201.12 (SW)
/Power/VFB: R205.1, U201.7 (VFB)
/Power/VIN: C201.1, P201.2 (PM), R209.1, U201.1 (VIN), U201.3 (~SHDN), U203.4
/Power/VIN_REG: R203.2, R209.2, R210.1, U201.2 (VIN_REG), U203.6
GND: BT201.2 (-), C201.2, C203.2, C205.2, C206.2, C207.2, C208.2, D201.1 (A), P201.1, R207.1, R210.2, U201.6 (TIMER), U201.13 (SGND), U202.3 (PGND), U202.7 (PS/SYNC), U202.9 (GND); also elsewhere on the board
unnamed: R205.2, R206.2, R207.2

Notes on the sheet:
Max charge current = 370mA
Trace for SW pin should be kept as short as possible
C2 should be kept as close to U1 as possible
Keep VFB traces as short as possible
SOLAR PANEL ARRAY

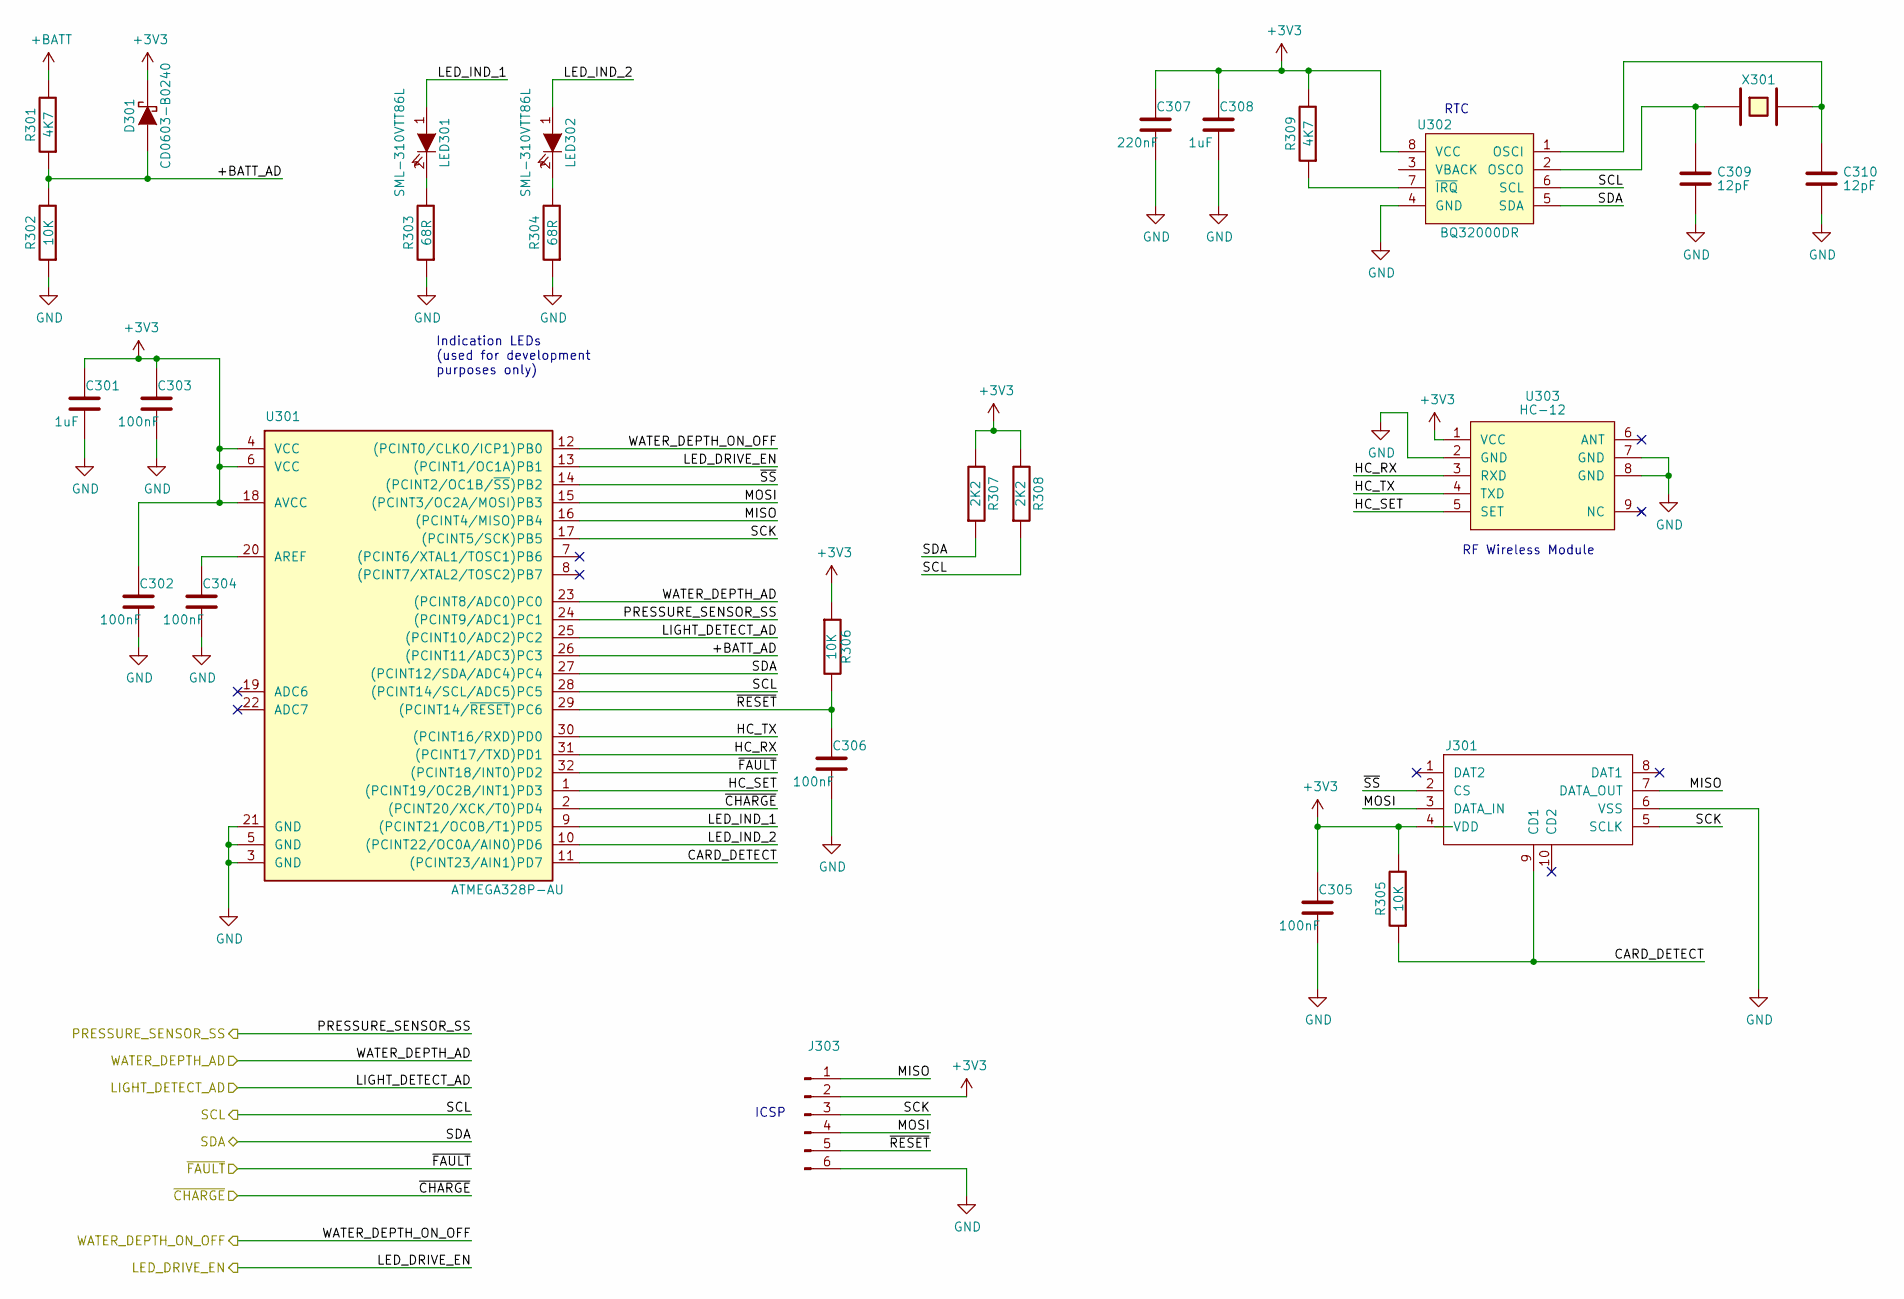
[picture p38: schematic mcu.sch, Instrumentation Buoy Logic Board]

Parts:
C301, C308: ECS00052; EC0603_C; Manfacturer Part Number GRM188R61H105KAALD
C302, C303, C304, C305, C306: ECS00075; EC0603_C; Manfacturer Part Number GRM188R71C104KA01D
C307: ECS00078; EC0603_C; Manfacturer Part Number GRM188R71A224KA01D
C309, C310: ECS00204; EC0603_C; Manfacturer Part Number GCM1885C2A120FA16D
D301: ECS00037; EC0603_DIODE; Manufacturer Part Number CD0603-B0240
J301: ECS00065; ECS00065F; Manufacturer Part Number 114-00841-68
J303: CONN6PROG
LED301, LED302: ECS00035; EC0603_LED; Manufacturer Part Number SML-310VTT86L
R301, R309: ECS00086; EC0603; Manufacturer Part Number CR0603-FX-4701ELF
R302, R305, R306: ECS00045; EC0603; Manufacturer Part Number ERJ3GEYJ103V
R303, R304: ECS00081; EC0603; Manufacturer Part Number CR0603-FX-68R0ELF
R307, R308: ECS00084; EC0603; Manufacturer Part Number MC0063W060312K2
U301: ECS00017; ECTQFP-32; Manufacturer Part Number ATMEGA328P-AU
U302: ECS00032; ECSOIC-8; Manufacturer Part Number BQ32000DR
U303: ECA00003; ECA00003F; Manufacturer Part Number HC-12
X301: ECS00005; ECS00005F; Manufacturer Part Number CC4V-T1A 32.768KHZ +-20PPM 9PF

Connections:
+BATT: R301.2; also elsewhere on the board
/LED Drive/LED_DRIVE_EN: U301.13 ((PCINT1/OC1A)PB1); also elsewhere on the board
/LED Drive/LIGHT_DETECT_AD: U301.25 ((PCINT10/ADC2)PC2); also elsewhere on the board
/Microcontroller/+BATT_AD: D301.1 (A), R301.1, R302.2, U301.26 ((PCINT11/ADC3)PC3)
/Microcontroller/CARD_DETECT: J301.9 (CD1), R305.1, U301.11 ((PCINT23/AIN1)PD7)
/Microcontroller/HC_RX: U301.31 ((PCINT17/TXD)PD1), U303.3 (RXD)
/Microcontroller/HC_SET: U301.1 ((PCINT19/OC2B/INT1)PD3), U303.5 (SET)
/Microcontroller/HC_TX: U301.30 ((PCINT16/RXD)PD0), U303.4 (TXD)
/Microcontroller/LED_IND_1: LED301.1 (A), U301.9 ((PCINT21/OC0B/T1)PD5)
/Microcontroller/LED_IND_2: LED302.1 (A), U301.10 ((PCINT22/OC0A/AIN0)PD6)
/Microcontroller/MISO: J301.7 (DATA_OUT), J303.1, U301.16 ((PCINT4/MISO)PB4)
/Microcontroller/MOSI: J301.3 (DATA_IN), J303.4, U301.15 ((PCINT3/OC2A/MOSI)PB3)
/Microcontroller/PRESSURE_SENSOR_SS: U301.24 ((PCINT9/ADC1)PC1); also elsewhere on the board
/Microcontroller/SCK: J301.5 (SCLK), J303.3, U301.17 ((PCINT5/SCK)PB5)
/Microcontroller/SCL: R308.1, U301.28 ((PCINT14/SCL/ADC5)PC5), U302.6 (SCL); also elsewhere on the board
/Microcontroller/SDA: R307.1, U301.27 ((PCINT12/SDA/ADC4)PC4), U302.5 (SDA); also elsewhere on the board
/Microcontroller/WATER_DEPTH_AD: U301.23 ((PCINT8/ADC0)PC0); also elsewhere on the board
/Microcontroller/WATER_DEPTH_ON_OFF: U301.12 ((PCINT0/CLKO/ICP1)PB0); also elsewhere on the board
/Microcontroller/~CHARGE: U301.2 ((PCINT20/XCK/T0)PD4); also elsewhere on the board
/Microcontroller/~FAULT: U301.32 ((PCINT18/INT0)PD2); also elsewhere on the board
/Microcontroller/~RESET: C306.1, J303.5, R306.2, U301.29 ((PCINT14/~RESET~)PC6)
/Microcontroller/~SS: J301.2 (CS), U301.14 ((PCINT2/OC1B/~SS~)PB2)
GND: C301.2, C302.2, C303.2, C304.2, C305.2, C306.2, C307.2, C308.2, C309.2, C310.2, J301.6 (VSS), J303.6, R302.1, R303.1, R304.1, U301.3 (GND), U301.5 (GND), U301.21 (GND), U302.4 (GND), U303.2 (GND), U303.7 (GND), U303.8 (GND); also elsewhere on the board
unnamed: C304.1, U301.20 (AREF)
unnamed: C309.1, U302.2 (OSCO), X301.1
unnamed: C310.1, U302.1 (OSCI), X301.2
unnamed: LED301.2 (K), R303.2
unnamed: LED302.2 (K), R304.2
unnamed: R309.1, U302.7 (~IRQ)

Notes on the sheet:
RTC
RF Wireless Module
ICSP
Indication LEDs (used for development purposes only)

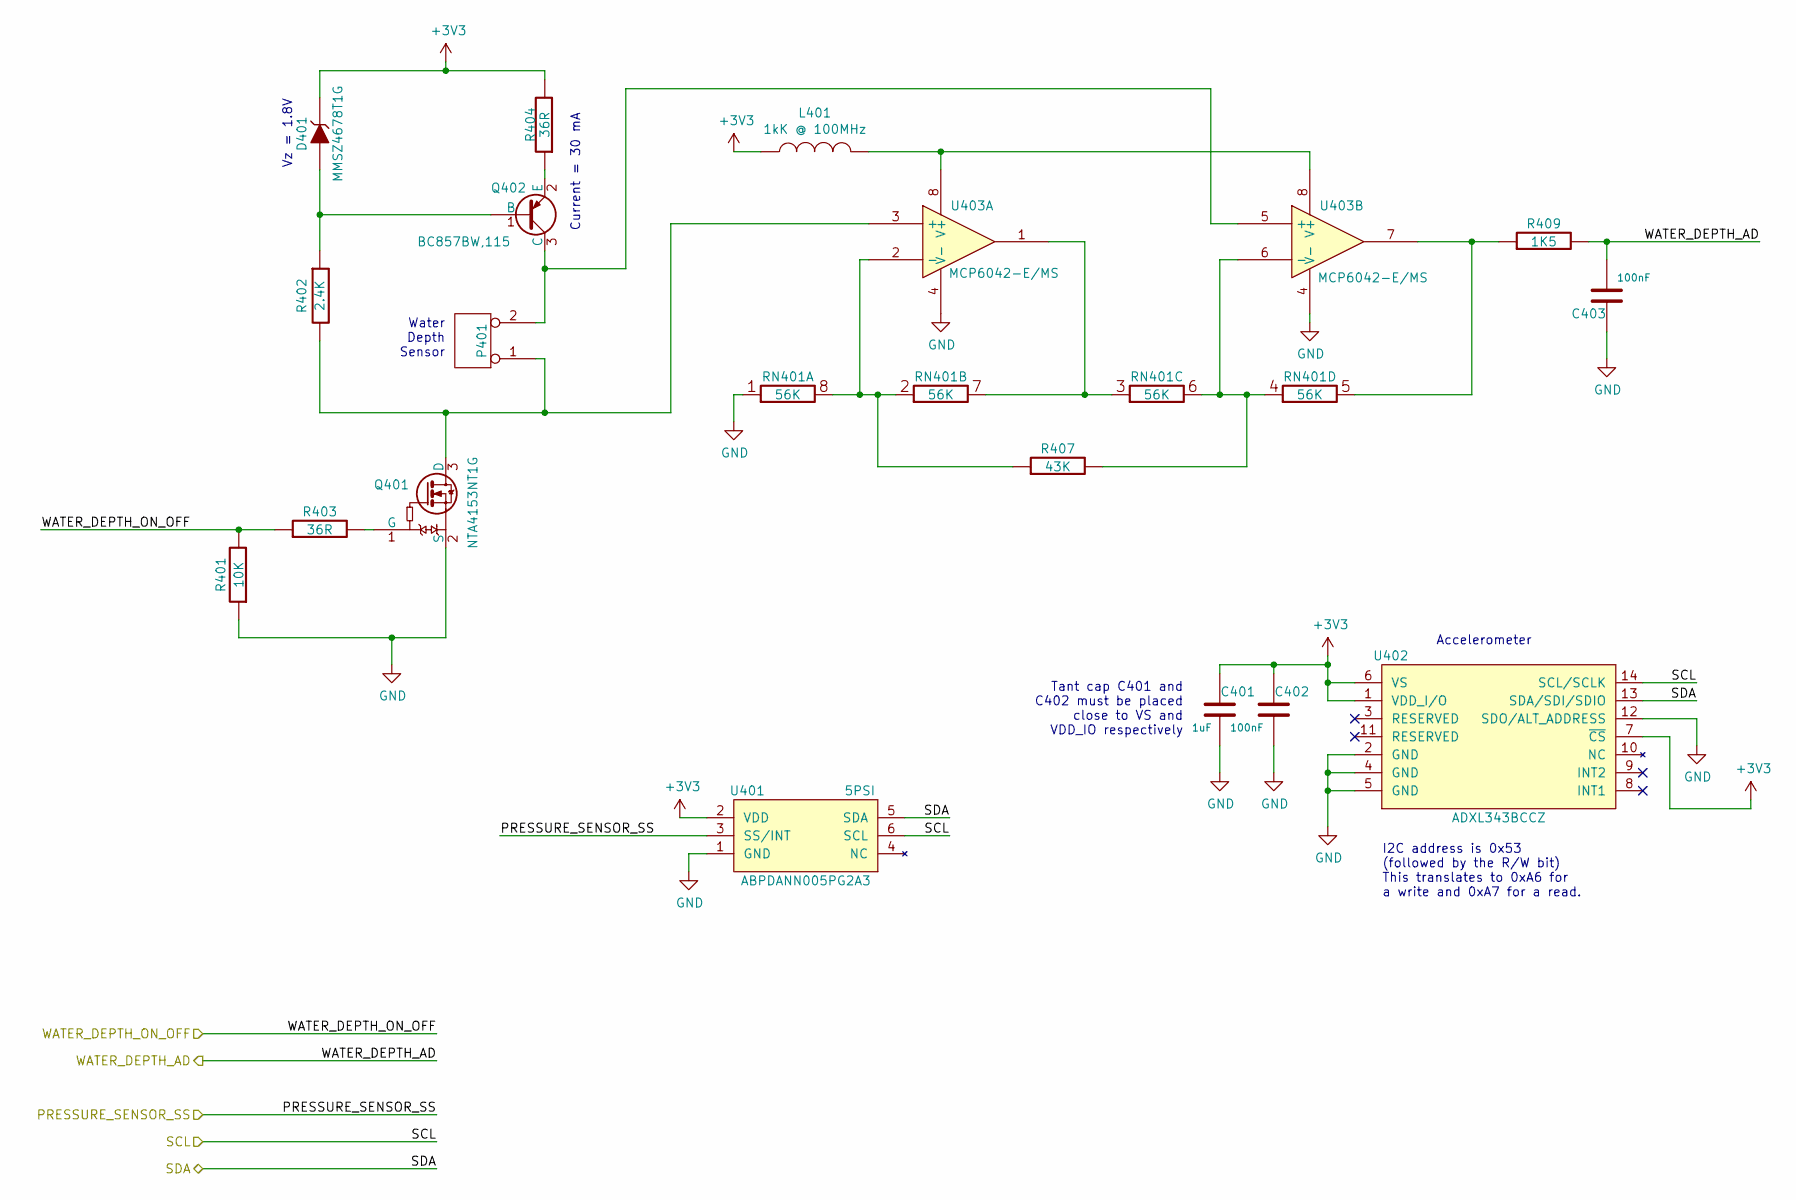
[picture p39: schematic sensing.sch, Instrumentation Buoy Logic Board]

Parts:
C401: ECS00052; EC0603_C; Manfacturer Part Number GRM188R61H105KAALD
C402, C403: ECS00075; EC0603_C; Manfacturer Part Number GRM188R71C104KA01D
D401: ECS00072; ECS00072F; Manufacturer Part Number MMSZ4678T1G
L401: ECS00074; EC0603_L; Manufacturer Part Number BLM18TG102TN1D
P401: ECS00067; ECS00067F; Manufacturer Part Number B2B-PH-SM4-TB(LF)(SN)
Q401: ECS00087; ECSOT416; Manufacturer Part Number NTA4153NT1G
Q402: ECS00073; ECSOT323; Manufacturer Part Number BC857BW,115
R401: ECS00045; EC0603; Manufacturer Part Number ERJ3GEYJ103V
R402: ECS00201; EC0603; Manufacturer Part Number ERJ-3EKF2401V
R403, R404: ECS00080; EC0603; Manufacturer Part Number CRCW060336R0FKEA
R407: ECS00203; EC0603; Manufacturer Part Number ERJ-3EKF4302V
R409: ECS00083; EC0603; Manufacturer Part Number CR0603-FX-1501ELF
RN401: ECS00206; ECS00206F; Manufacturer Part Number TC164-FR-0756KL
U401: ECS00114; ECS00114F; Manufacturer Part Number ABPDANN005PG2A3
U402: ECS00016; ECS00016F; Manufacturer Part Number ADXL343BCCZ
U403: ECS00030; ECMSOP-8; Manufacturer Part Number MCP6042-E/MS

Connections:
/Microcontroller/PRESSURE_SENSOR_SS: U401.3 (SS/INT); also elsewhere on the board
/Microcontroller/SCL: U401.6 (SCL), U402.14 (SCL/SCLK); also elsewhere on the board
/Microcontroller/SDA: U401.5 (SDA), U402.13 (SDA/SDI/SDIO); also elsewhere on the board
/Microcontroller/WATER_DEPTH_AD: C403.2, R409.2; also elsewhere on the board
/Microcontroller/WATER_DEPTH_ON_OFF: R401.2, R403.1; also elsewhere on the board
GND: C401.2, C402.2, C403.1, Q401.2 (S), R401.1, RN401.1, U401.1 (GND), U402.2 (GND), U402.4 (GND), U402.5 (GND), U402.12 (SDO/ALT_ADDRESS), U403.4 (V-); also elsewhere on the board
unnamed: D401.2 (A), Q402.1 (B), R402.1
unnamed: L401.2, U403.8 (V+)
unnamed: P401.1, Q401.3 (D), R402.2, U403.3 (+)
unnamed: P401.2 (PM), Q402.3 (C), U403.5 (+)
unnamed: Q401.1 (G), R403.2
unnamed: Q402.2 (E), R404.1
unnamed: R407.1, RN401.2, RN401.8, U403.2 (-)
unnamed: R407.2, RN401.4, RN401.6, U403.6 (-)
unnamed: R409.1, RN401.5, U403.7
unnamed: RN401.3, RN401.7, U403.1

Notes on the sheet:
Accelerometer
I2C address is 0x53 (followed by the R/W bit) This translates to 0xA6 for a write and 0xA7 for a read.
Water Depth Sensor
Vz = 1.8V
Current = 30 mA
Tant cap C401 and C402 must be placed close to VS and VDD_IO respectively

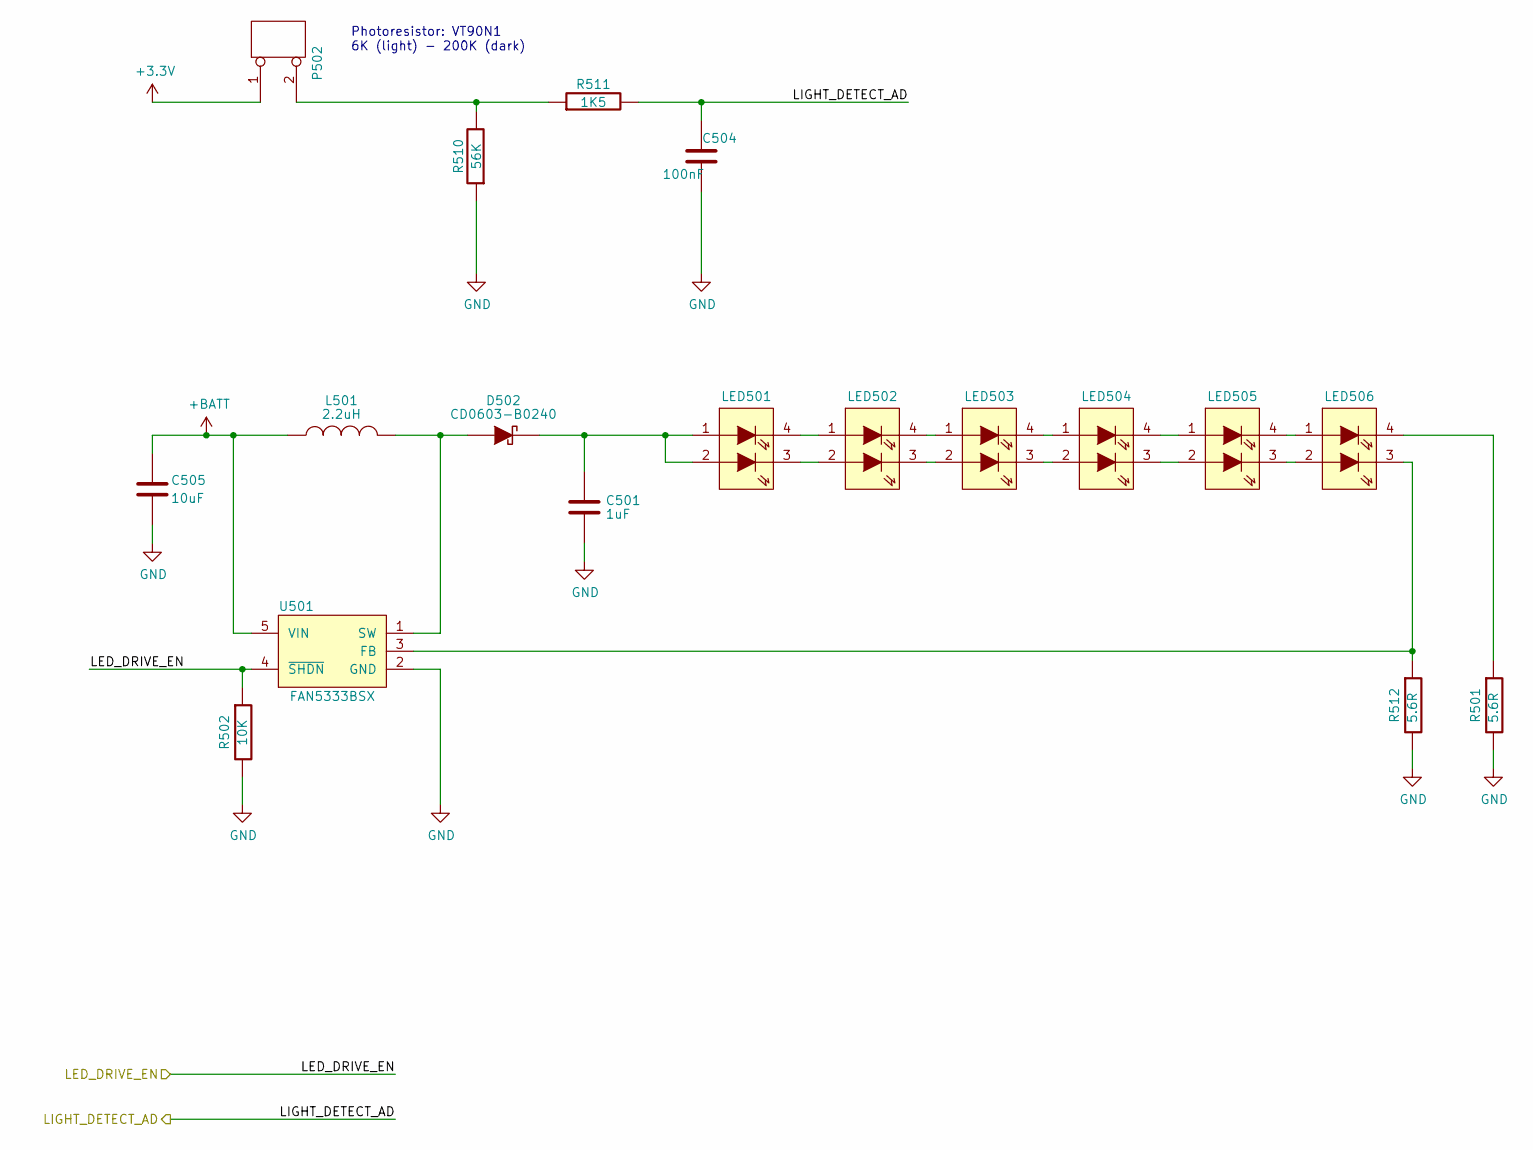
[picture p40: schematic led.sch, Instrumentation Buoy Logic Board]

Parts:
C501: ECS00052; EC0603_C; Manfacturer Part Number GRM188R61H105KAALD
C504: ECS00075; EC0603_C; Manfacturer Part Number GRM188R71C104KA01D
C505: ECS00051; EC1206; Manfacturer Part Number GRM31CR61H106KA12L
D502: ECS00037; EC0603_DIODE; Manufacturer Part Number CD0603-B0240
L501: ECS00210; VLS3015CX-2R2M-1; Manufacturer Part Number VLS3015CX-2R2M-1
LED501, LED502, LED503, LED504, LED505, LED506: ECS00208; CLV1A-FKB; Manufacturer Part Number CLA2A-WKW-CYBZ0343TR-ND
P502: ECS00004; ECS00004F; Manufacturer Part Number 22-28-4020
R501, R512: ECS00213; EC0603; Manufacturer Part Number ERJ-3RQF5R6V
R502: ECS00045; EC0603; Manufacturer Part Number ERJ3GEYJ103V
R510: ECS00085; EC0603; Manufacturer Part Number CRCW060356K0FKEAHP
R511: ECS00083; EC0603; Manufacturer Part Number CR0603-FX-1501ELF
U501: ECS00207; ECSOT23-5; Manufacturer Part Number FAN5333BSX

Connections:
+BATT: C505.1, L501.1, U501.5 (VIN); also elsewhere on the board
/LED Drive/LED_DRIVE_EN: R502.1, U501.4 (~SHDN); also elsewhere on the board
/LED Drive/LIGHT_DETECT_AD: C504.1, R511.2; also elsewhere on the board
GND: C501.2, C504.2, C505.2, R501.2, R502.2, R510.1, R512.2, U501.2 (GND); also elsewhere on the board
unnamed: C501.1, D502.2 (K), LED501.1 (A), LED501.2 (A)
unnamed: D502.1 (A), L501.2, U501.1 (SW)
unnamed: LED501.3 (K), LED502.2 (A)
unnamed: LED501.4 (K), LED502.1 (A)
unnamed: LED502.3 (K), LED503.2 (A)
unnamed: LED502.4 (K), LED503.1 (A)
unnamed: LED503.3 (K), LED504.2 (A)
unnamed: LED503.4 (K), LED504.1 (A)
unnamed: LED504.3 (K), LED505.2 (A)
unnamed: LED504.4 (K), LED505.1 (A)
unnamed: LED505.3 (K), LED506.2 (A)
unnamed: LED505.4 (K), LED506.1 (A)
unnamed: LED506.3 (K), R512.1, U501.3 (FB)
unnamed: LED506.4 (K), R501.1
unnamed: P502.2 (PM), R510.2, R511.1

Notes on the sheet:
Photoresistor: VT90N1 6K (light) - 200K (dark)

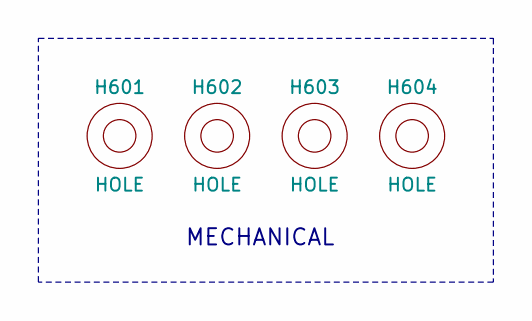
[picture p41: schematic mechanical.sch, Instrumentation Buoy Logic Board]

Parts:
H601, H602, H603, H604: HOLE; HOLE_5.5MM

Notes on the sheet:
MECHANICAL

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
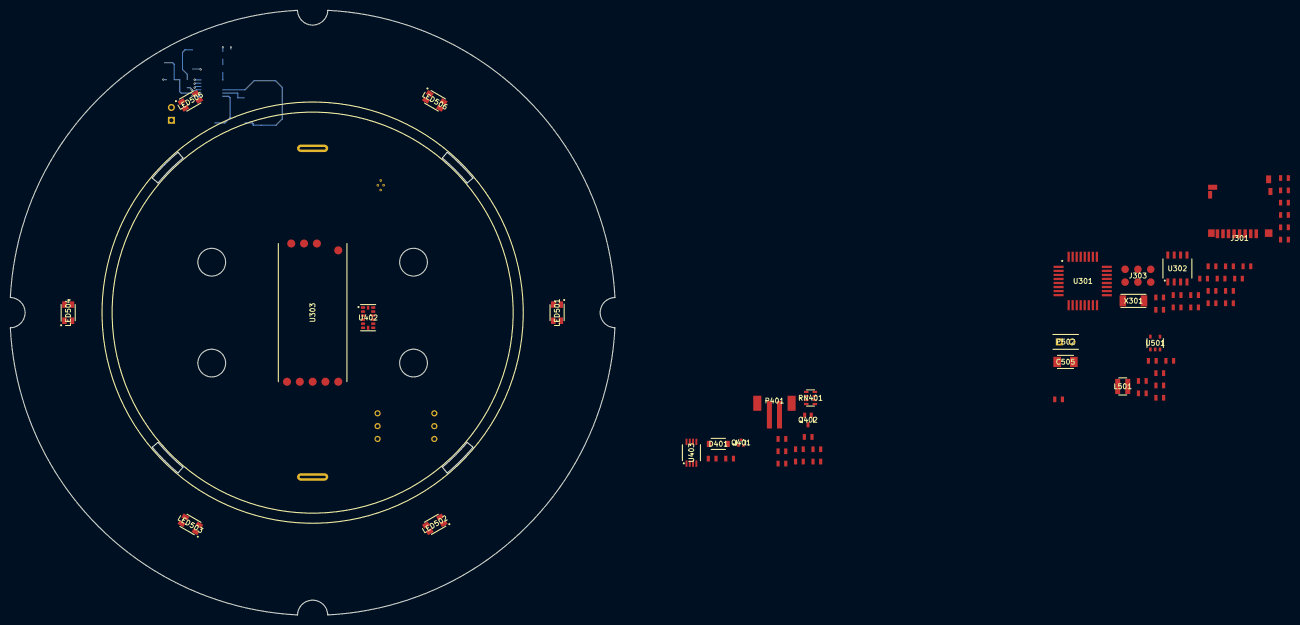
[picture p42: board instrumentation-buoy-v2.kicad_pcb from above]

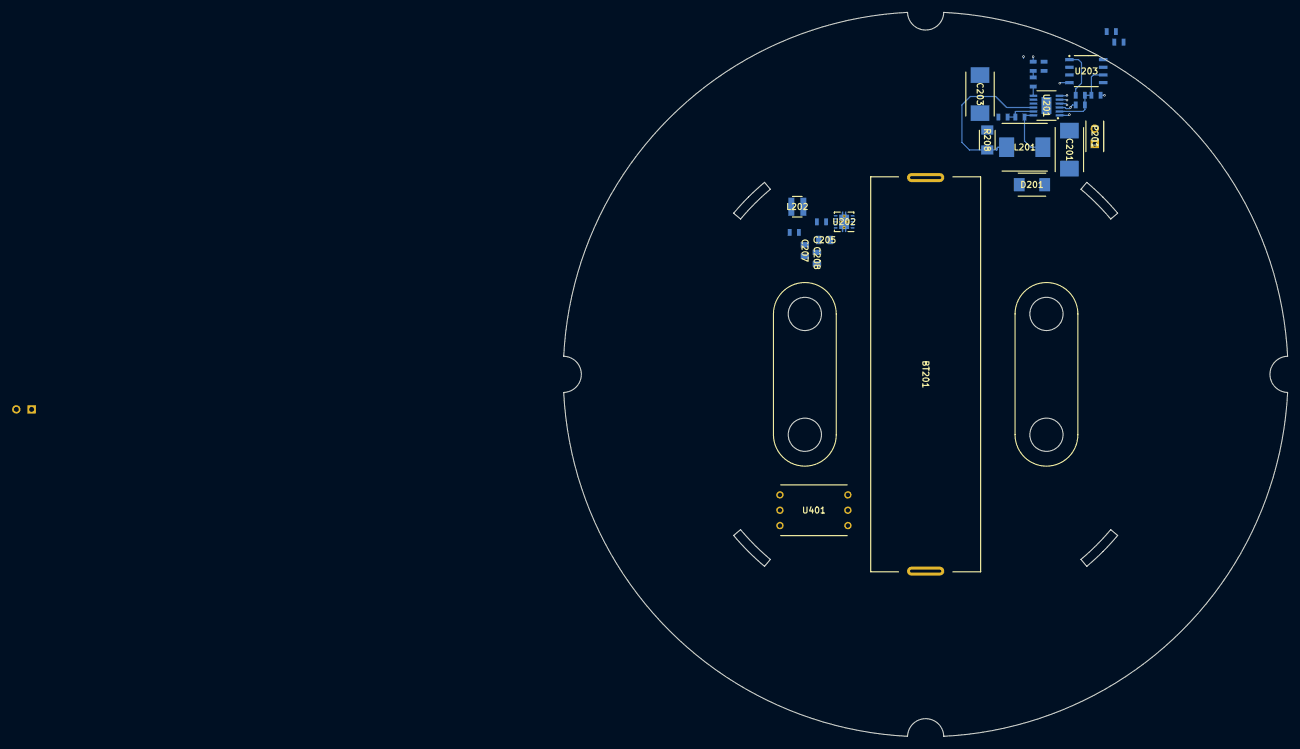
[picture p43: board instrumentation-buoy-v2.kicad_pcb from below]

Board: 4 copper layers, 119.9 x 119.8 mm, 94 parts (27 on the bottom side), 66 nets.

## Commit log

2020-05-15 First commit.
    [board_outline.dxf, instrumentation-buoy-v2.kicad_pcb, instrumentation-buoy-v2.sch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]
2020-05-25 Commiting BOM and updated .gitignore file.
    [bom.xlsx]
2020-05-25 Adding schematic jpg files, updated BOM and added BOM to README markdown as well. Updated top level README to formate the tecnical documentation better.
    [bom-instrumentation-buoy-v2.xlsx, bom.xlsx]
